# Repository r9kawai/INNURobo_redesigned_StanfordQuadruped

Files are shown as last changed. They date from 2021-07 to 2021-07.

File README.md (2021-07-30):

# INNURobo_redesigned_StanfordQuadruped
"INNURobo" is redesigned  StanfordQuadruped "Pupper" to easily and cheap buide.  
https://youtu.be/vSy8UrXWn40
  
・Design improvement　設計改良点  
・3D printed parts only.　3Dプリントパーツのみで構成  
・We can part sourcing in Amazon only.　アマゾンで入手可能な部品のみ  
・Non use exclusive PCB.　専用基板不使用  
・Non use CFRP cutting plate. CFRP板カット品不要  
・More cheaper.　低コスト化  
  
Stanford Pupper  https://stanfordstudentrobotics.org/pupper  
https://github.com/stanfordroboticsclub/StanfordQuadruped

Design on FreeCAD  
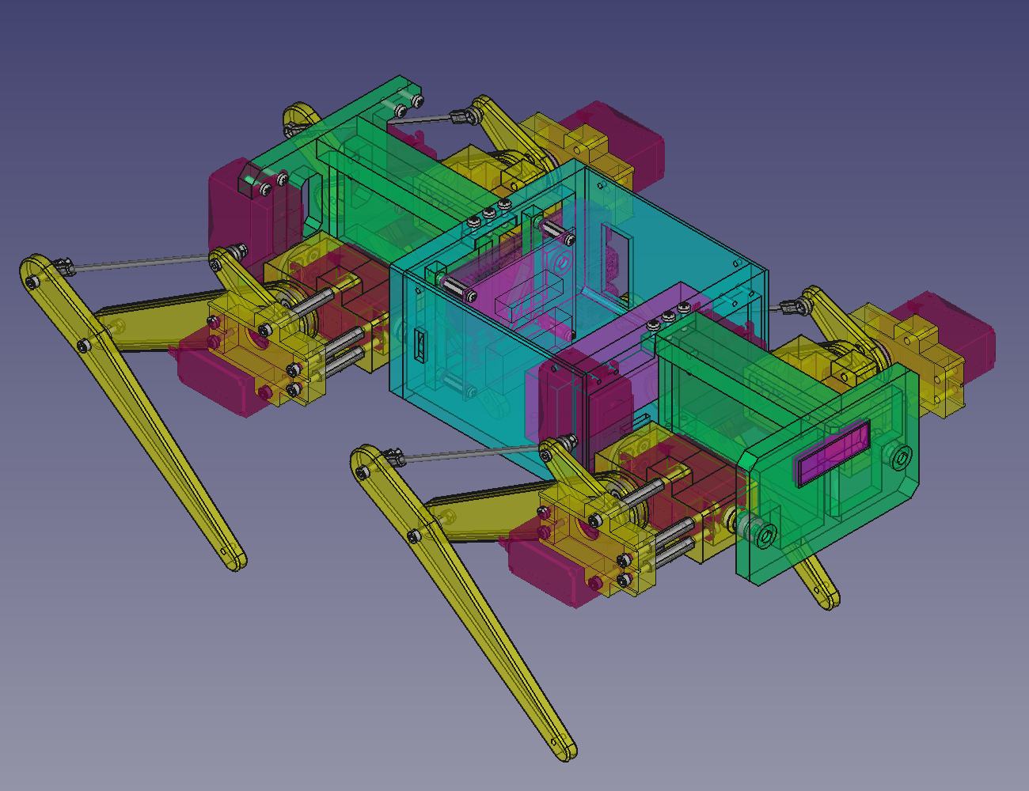
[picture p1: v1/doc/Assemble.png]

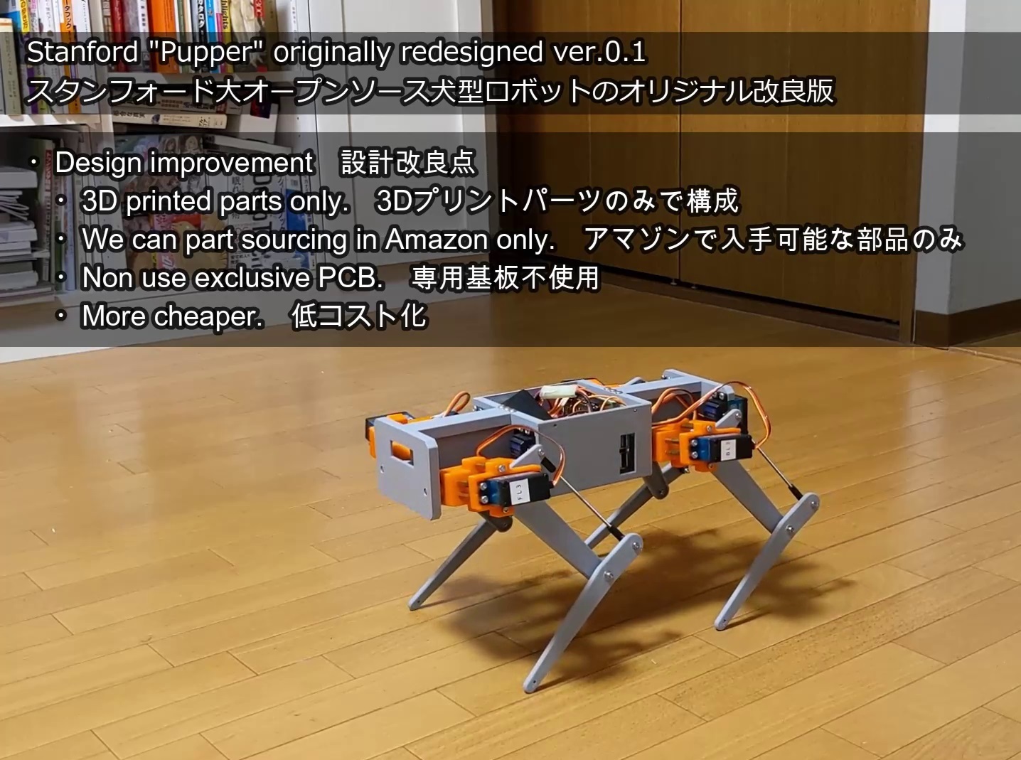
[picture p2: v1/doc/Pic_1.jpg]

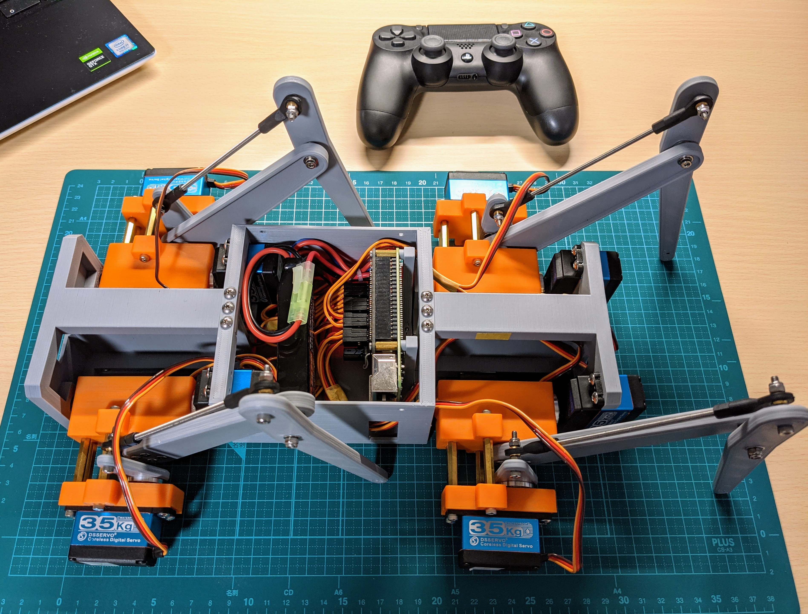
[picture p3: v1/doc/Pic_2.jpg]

  
Stanford Pupper original  
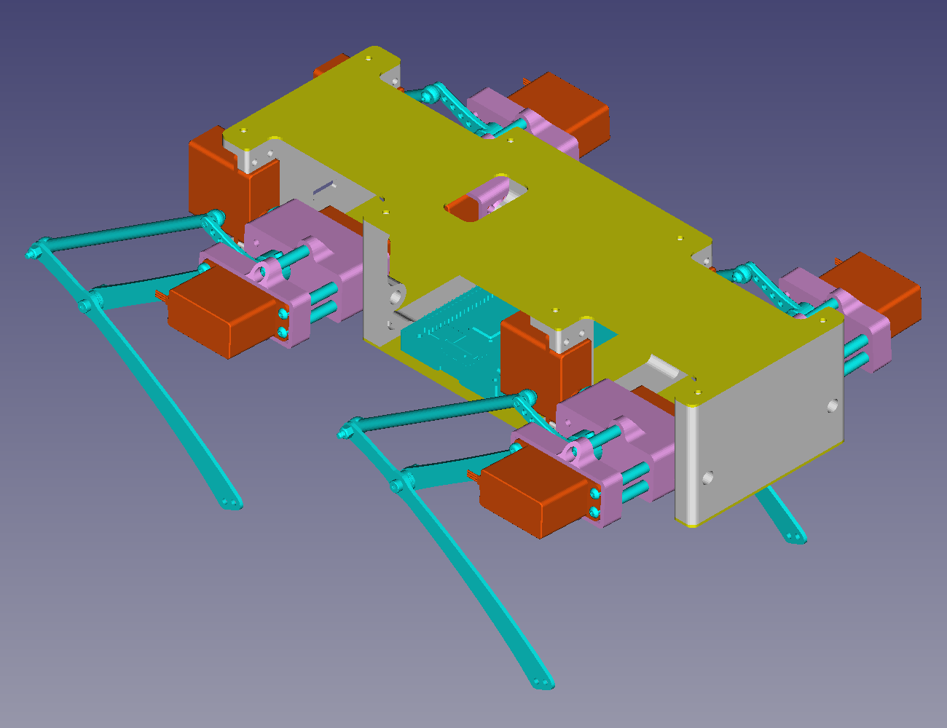
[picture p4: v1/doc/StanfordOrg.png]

  
PCB circuit  
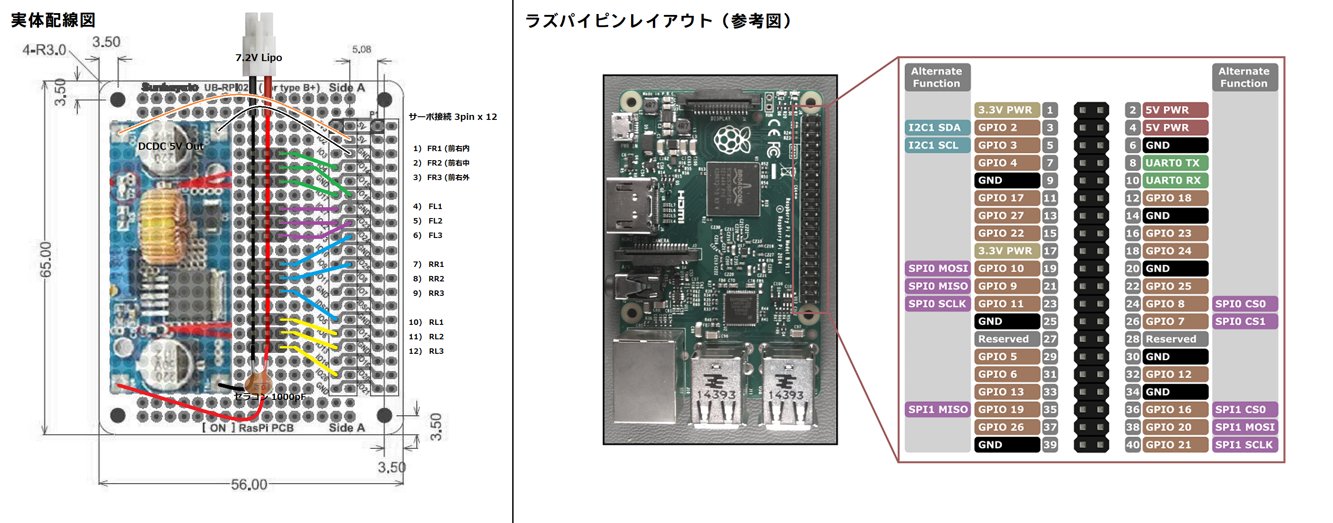
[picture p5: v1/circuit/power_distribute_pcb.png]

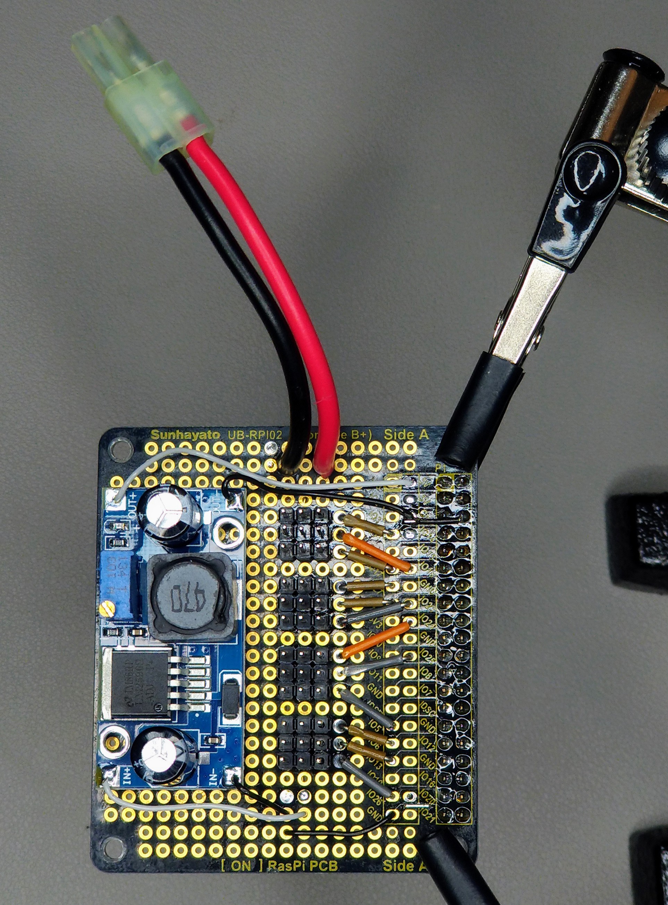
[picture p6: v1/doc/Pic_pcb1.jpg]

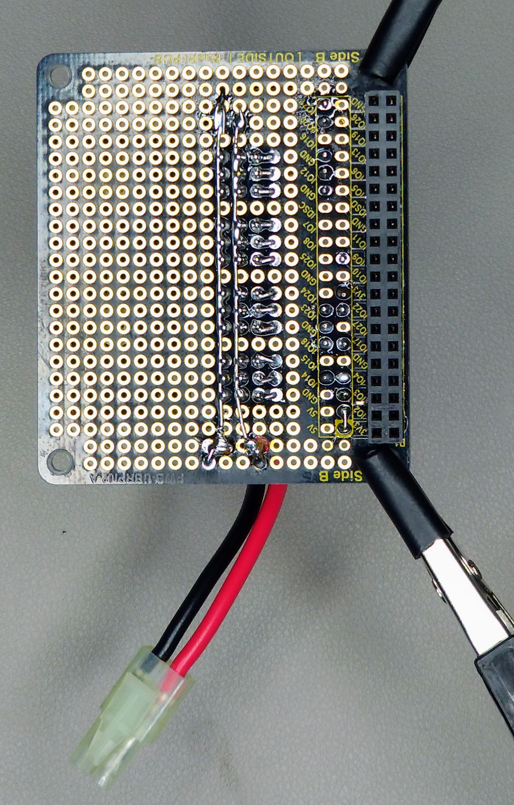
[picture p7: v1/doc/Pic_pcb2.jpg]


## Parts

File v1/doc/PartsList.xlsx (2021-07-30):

※AliExpressを利用するとずっと安く購入できます。 |  |  |  | We can save money at AliExpress.
INNURobo v1 PartsList 部品表
 |  |  |  | 43 | 種 kinds |  |  |  |  | 293 | 点 total
 | 区分 | Section |  | 品名 | Name |  |  |  |  | 数量 Quantity
 | 3DプリントPLA |  | フレーム | フロントフレーム |  | Front flame |  |  |  | 1 | 0.25mmレイヤーでの印刷を推奨
 | 3D print PLA |  | Frame | センターフレーム |  | Center flame |  |  |  | 1 | recommend layer 0.25mm
 |  |  |  | バックフレーム |  | Rear flame |  |  |  | 1
 |  |  |  | ラズパイマウンタ |  | RaspPi mounter |  |  |  | 1
 |  |  | 足 | アッパーサーボホルダ |  | Upper servo holder |  |  |  | 4
 |  |  | leg | ロワーサーボホルダ |  | Lower servo holder |  |  |  | 4
 |  |  |  | アッパーレッグ |  | Upper leg |  |  |  | 4
 |  |  |  | ロワーレッグ |  | Lower leg |  |  |  | 4
 |  |  |  | ロワーレッグホーン |  | Lower leg horn |  |  |  | 4
 | アクチュエーター |  | Servo | サーボモーターDS3235 |  |  |  |  |  | 12 | https://www.amazon.co.jp/dp/B08D1QLPX4/
 |  |  |  |  | The servo is most cost factor, should buy from china buyer. |  |  |  |  |  | ↑最大のコスト要因、日本アマゾンで買うと高いので勧めない。
 | メイン基板 |  | Main PCB | ラズベリーパイ4 |  | RasPi4 |  |  |  | 1
 |  |  |  | ラズベリーパイ4用ヒートシンク |  |  | heat sink |  |  | 1
 |  |  |  | microSDカード16GB |  |  |  |  |  | 1
 |  |  |  | M2.5六角スペーサー12mm+6mm(ネジ－ネジ穴) |  |  |  | spacer |  | 4 | https://www.amazon.co.jp/dp/B08KFX9DG2/
 |  |  |  | M2.5x6プラスネジ |  | plus screw |  |  |  | 4
 | パワー基板 |  | PowerPCB | サンハヤトラズベリーパイ用ユニバーサル基板 |  |  |  |  |  | 1 | https://www.amazon.co.jp/dp/B00TY12WH0/
 |  |  |  |  | SUNHAYATO UB-RPI02 |  |  | Raspi on universal PCB
 |  |  |  | DCDCコンバータ降圧3A |  |  |  | DCDC converter |  | 1 | https://www.amazon.co.jp/gp/product/B010RYGGJC/
 |  |  |  | 電動ガン用バッテリーコネクタ（ミニ |  |  |  | connecter |  | 1 | https://www.amazon.co.jp/gp/product/B07TSPL959/
 |  |  |  | ジャンパ線材 |  |  | Jump wires
 |  |  |  | 錫めっき線材
 |  |  |  | ACアダプタ用線材 |  |  | Power wires
 |  |  |  | ACアダプタ用丸コネクタメス |  |  |  |  |  | 1
 |  |  |  | DIPピンヘッダ3ピン12列 |  |  | DIP pinheader |  |  | 1 | https://www.amazon.co.jp/dp/B017IPWYDK/
 | コントローラー |  |  | PS4 DualShock2 |  |  |  |  |  | 1
 | バッテリー |  |  | 電動ガン用7.4VLipoバッテリー |  |  | lipo 2s |  |  | 1 | https://www.amazon.co.jp/gp/product/B07HDVZQGB/
 | メカ部品 | 締結ネジ・ナット |  | M3x16六角穴ボルト |  |  | hex head bolt |  |  | 32 | (8x足4) | https://www.amazon.co.jp/dp/B002A5NUQ4/
 |  | mecha bolt nut |  | M3x8六角穴皿型ボルト |  |  | hex plate face bolt |  |  | 48 | (4xサーボ数3x足4)
 |  |  |  | M3x10なべ型タッピング |  |  | tapping screw |  |  | 46 | (8x足4)+(3xフレーム4個所)+(基板用2)
 |  |  |  |  |  |  |  |  |  |  |  | https://www.amazon.co.jp/dp/B002A5NIIO/
 |  |  |  | M3六角スペーサー25mm(ネジ穴-ネジ穴) |  |  |  | spacer |  | 16 | (4x足4) | https://www.amazon.co.jp/gp/product/B013G1H6HO/
 |  | 5mm股関節軸 |  | M5x16六角穴皿型ボルト |  |  | hex plate face bolt |  |  | 4 | (足4)
 |  | 5mm axis |  | ベアリング5x11x5 |  |  | 内径5外径11厚5mm |  | bearing | 4
 |  |  |  | M5六角ナット(3種) |  |  | hex nut |  |  | 4
 |  |  |  | M5ワッシャー |  |  | washer |  |  | 8 | (2x足4)
 |  | 3mm膝軸 |  | スラストベアリング4x10x4 |  |  | thrust bearing |  |  | 4 | (足4) | https://www.amazon.co.jp/dp/B0836VJL9K/
 |  | 3mm axis |  | M3x20六角穴ボルト |  |  | hex bolt |  |  | 12 | (3x足4)
 |  |  |  | M3六角ナット |  |  | hex nut |  |  | 8 | (2x足4)
 |  |  |  | M3六角ナイロンナット |  |  | hex nylon nut |  |  | 12 | (3x足4) | https://www.amazon.co.jp/dp/B07MPDVGZW/
 |  |  |  | M3ワッシャー |  |  | washer |  |  | 8 | (2x足4)
 |  | サーボホーン |  | 丸型アルミサーボホーン |  |  | round shape servo horn |  |  | 12 | (3x足4) | https://www.amazon.co.jp/gp/product/B07P5JCGK1/
 |  | servo horn |  | M3x6六角穴ボルト |  |  | hex bolt |  |  | 8 | (サーボ数3-1x足4)
 |  | リンケージ |  | M3x100mmネジロッド |  |  | screw rod |  |  | 4 | (足4) | https://www.amazon.co.jp/gp/product/B071HJQBK3/
 |  | linkage |  | M3x29mmボールタイロッド |  |  | ball rod |  |  | 8 | (2x足4) | https://www.amazon.co.jp/gp/product/B07PTPC6S3
 |  |  |  | リンケージ長さ調整治具 |  |  | linkage adjust JIGU |  |  | 1
 |  |  |  |  | STL同梱 |  |  | in STL

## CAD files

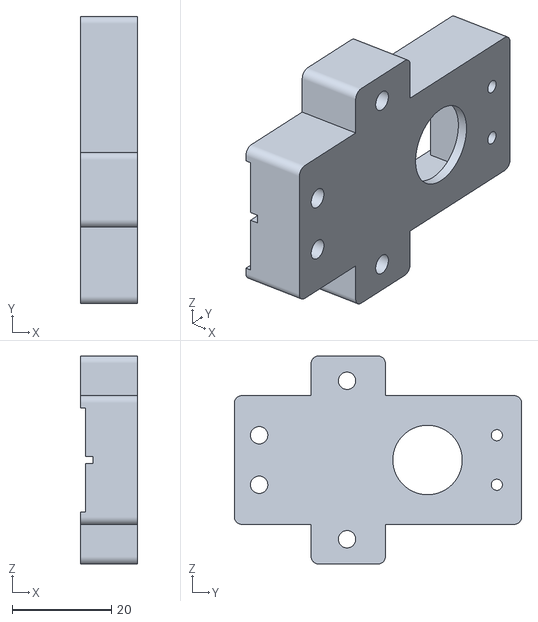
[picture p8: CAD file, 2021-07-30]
v1/stl/INNURobo_v1_0-INNURoboOutHip_x4.stl
11.5 x 58.0 x 42.0

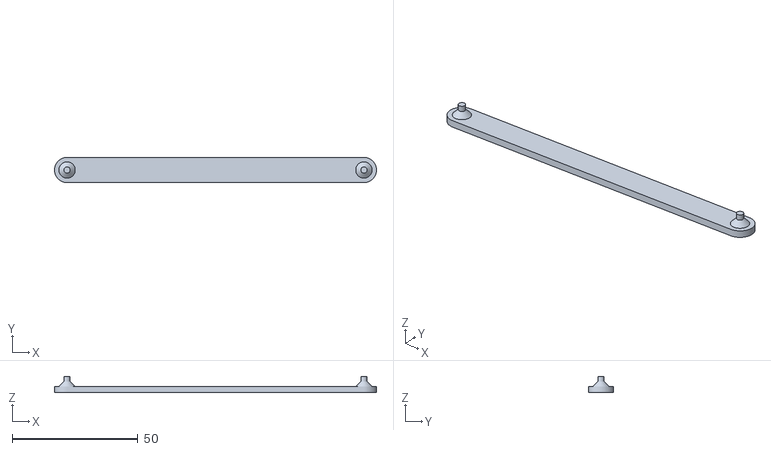
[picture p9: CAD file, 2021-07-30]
v1/stl/INNURobo_v1_0-LinkRod_JIGU_118mm.stl
128.0 x 10.0 x 6.50

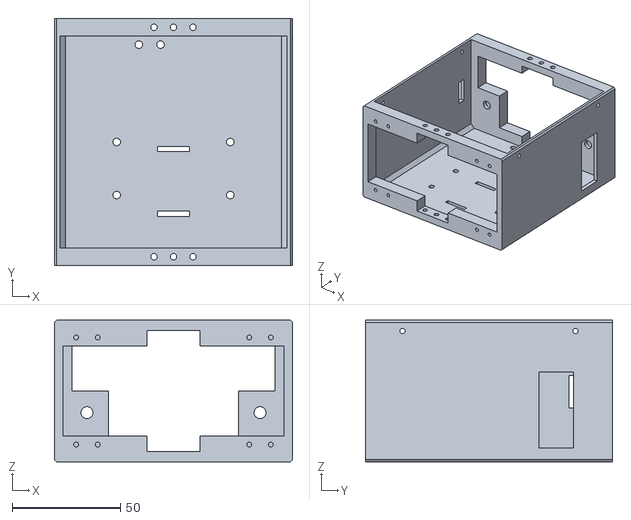
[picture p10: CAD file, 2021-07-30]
v1/stl/INNURobo_v1_0-INNURoboC_Frame.stl
110.0 x 114.0 x 65.5

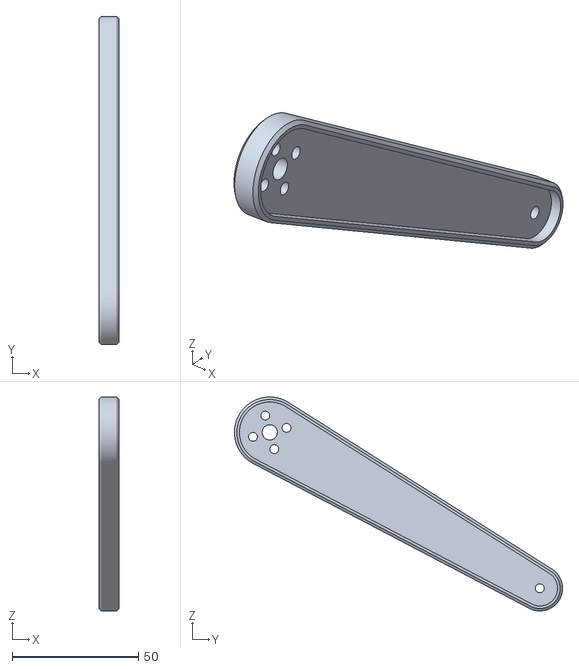
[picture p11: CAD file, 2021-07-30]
v1/stl/INNURobo_v1_0-INNURoboUpperLeg_x4.stl
8.00 x 130.0 x 84.7

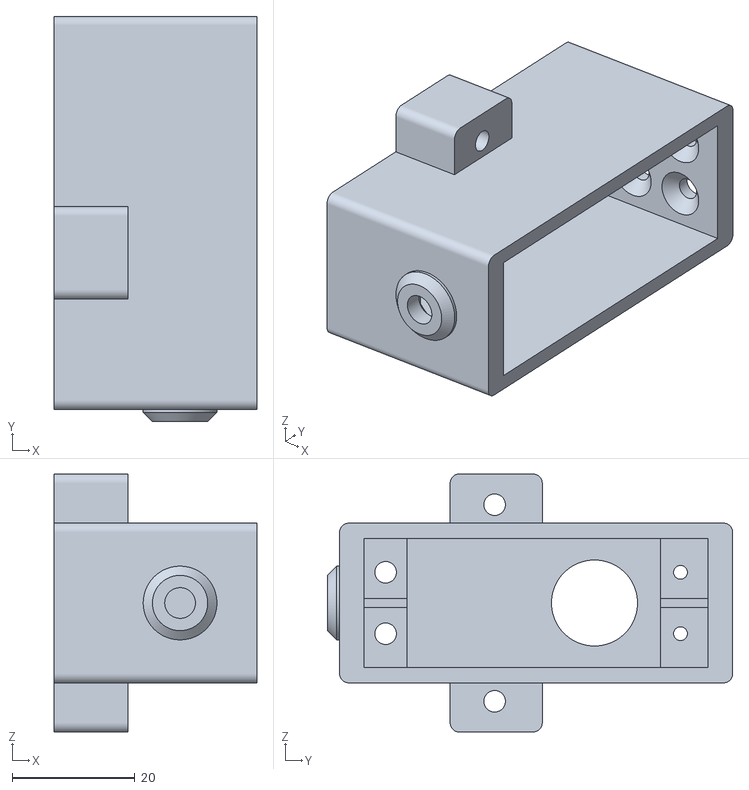
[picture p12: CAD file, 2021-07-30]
v1/stl/INNURobo_v1_0-INNURoboInHip_x4.stl
33.0 x 66.0 x 42.0

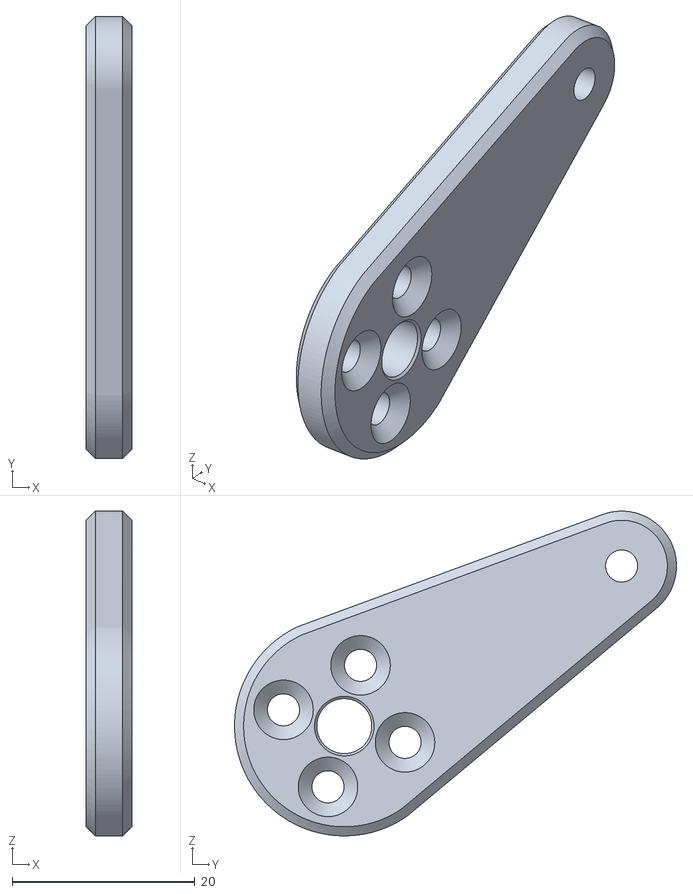
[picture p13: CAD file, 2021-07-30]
v1/stl/INNURobo_v1_0-INNURoboDHorn_x4.stl
5.00 x 48.3 x 35.5

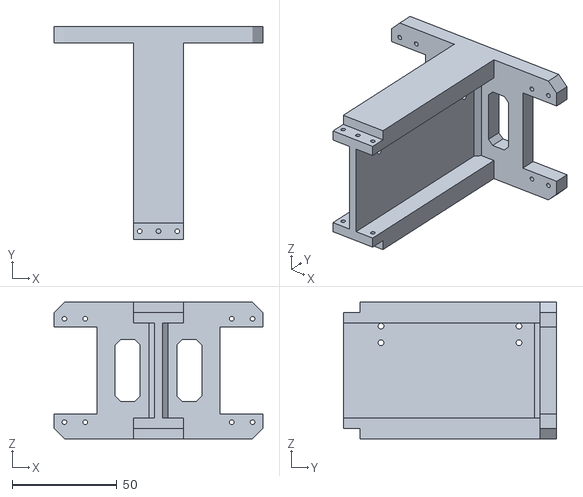
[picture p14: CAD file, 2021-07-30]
v1/stl/INNURobo_v1_0-INNURoboR_Frame.stl
100.0 x 102.0 x 65.5

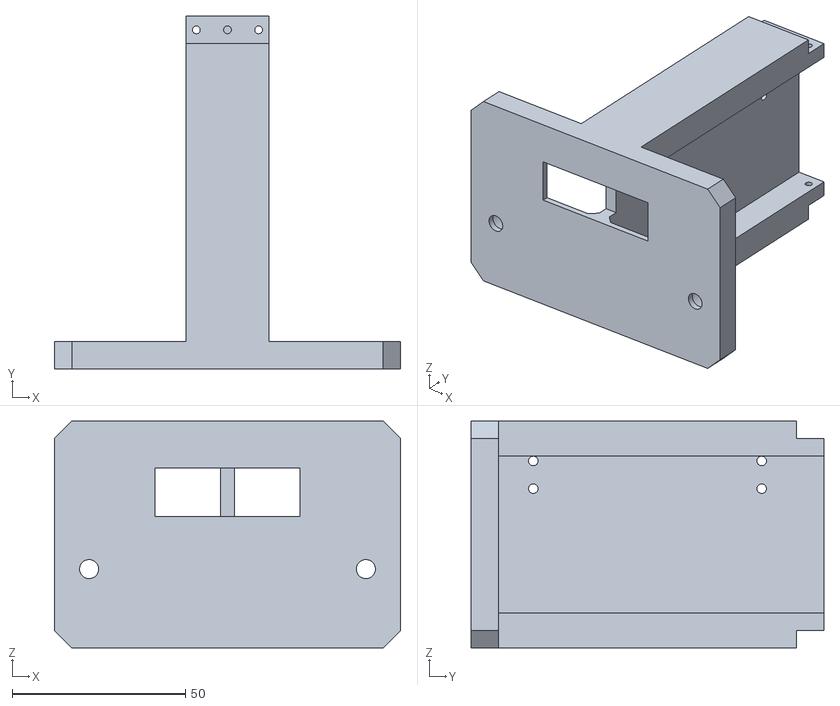
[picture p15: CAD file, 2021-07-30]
v1/stl/INNURobo_v1_0-INNURoboF_Frame.stl
100.0 x 102.0 x 65.5

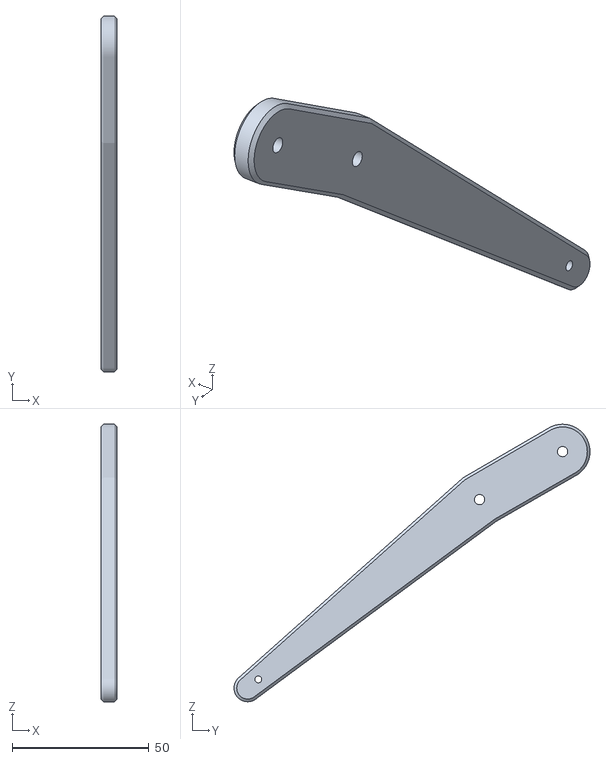
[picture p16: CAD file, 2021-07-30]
v1/stl/INNURobo_v1_0-INNURoboLowerLeg_x4.stl
6.00 x 130.0 x 101.3

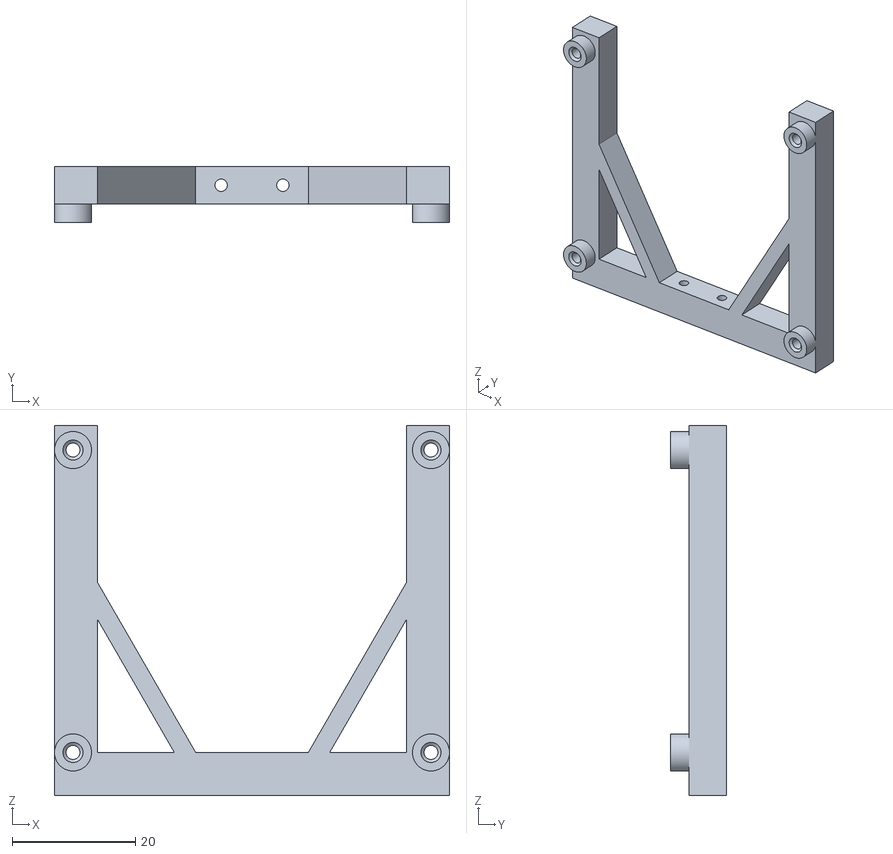
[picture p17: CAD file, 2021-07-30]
v1/stl/INNURobo_v1_0-INNURoboPiMount.stl
64.0 x 9.00 x 60.0
